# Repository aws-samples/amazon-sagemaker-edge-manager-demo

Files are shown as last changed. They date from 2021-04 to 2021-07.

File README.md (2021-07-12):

# SageMaker Edge Manager demo: Mini wind turbine farm
## A DIY project to explore ML@Edge with SageMaker

 > This repo is part of the blog post [Monitor and Manage Anomaly Detection Models on a fleet of Wind Turbines with Amazon SageMaker Edge Manager](https://aws.amazon.com/blogs/machine-learning/monitor-and-manage-anomaly-detection-models-on-a-fleet-of-wind-turbines-with-amazon-sagemaker-edge-manager/). If you want to implement the full solution, please follow the configuration steps described in the blog post and prepare your AWS account.

**TL:DR**: [Mini 3D printed wind turbines - assembling instructions](ASSEMBLING.md)

> **2021-06-18 NEW**: With the release of SageMaker Edge Manager support in AWS Greengrass v2, we have created a separate branch of this demo. Check it out by doing `git pull & git checkout greengrass`

**DISCLAIMER**: If you don't have a 3D printer or the skills to build your own fleet of wind turbines, don't worry. You can still run the application in demonstration mode. Also, there is a [SageMaker Edge Manager Workshop](https://github.com/aws-samples/amazon-sagemaker-edge-manager-workshop) where you will be able to run a similar experiment but with a Simulator! :)

In this project you'll see how to build a **Mini Wind Turbine Farm**, to experiment with Machine Learning (@ Edge). With a 3D printer and some electronic components you can create a mini Wind Turbine with sensors and a small generator. This project is not intended to be a real-life electricity generator. It's just a device for testing/experimenting real-time and low latency machine learning on edge devices. It was created to demonstrate the capabilities of Amazon SageMaker Edge Manager.

[Amazon SageMaker Edge Manager](https://aws.amazon.com/sagemaker/edge-manager/) allows you to optimize, secure, monitor, and maintain ML models on fleets of smart cameras, robots, personal computers, industrial equipments, mobile devices and more. Using [Amazon SageMaker Edge Manager](https://aws.amazon.com/sagemaker/edge-manager/), you can manage the lifecycle of each ML model on each device in your device fleets for up to thousands or millions of devices. The service provides a software **agent that runs on edge devices** and a management interface in the AWS console. 

Using a Machine Learning model (Autoencoder) you can analyze the turbine sensors data and detect anomalies. This technique is important to improve the maintenance process and reduce the operational cost. Click on the image bellow to see a video of the Wind Turbine Farm running.

<p align="center">
<a href="https://aws-ml-blog.s3.amazonaws.com/artifacts/monitor-manage-anomaly-detection-model-wind-turbine-fleet-sagemaker-neo/wind_farm.mp4">
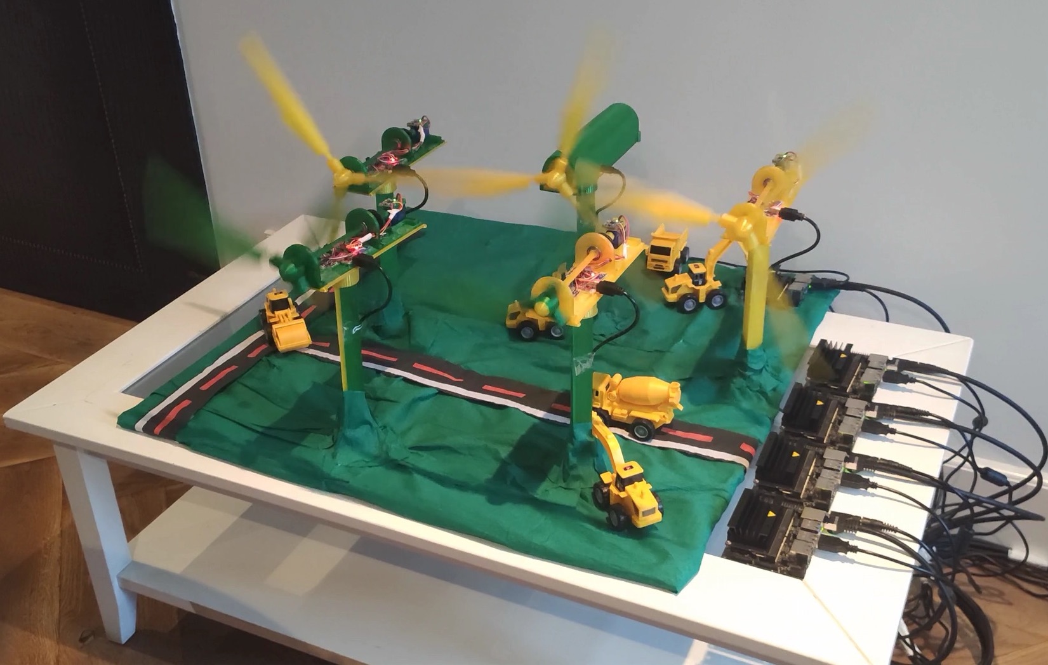
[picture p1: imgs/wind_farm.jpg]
 
</a>
</p>

### Solution architecture
This is the reference architecture of this solution. The idea is to use <a href="https://aws.amazon.com/sagemaker/">Amazon SageMaker</a> to train an [AutoEncoder](https://en.wikipedia.org/wiki/Autoencoder) using the Turbine sensors data. Each edge device (Jetson Nano) has a SageMaker Edge Agent (edge) running on it. The agents are connected to devices registered to a device fleet on SageMaker Edge Manager (cloud). Also, for each edge device there is an IoT Thing. This is required by [the application](/04_EdgeApplication/README.md) that runs on the edge device to send logs to the cloud and for the OTA model update mechanism. By using SageMaker Agent CaptureData, the application collects some metrics from the predictions and sends to an S3 bucket (via agent). Lambda functions process the model metrics from S3 and the app logs from the MQTT Topic and ingests it to Elasticsearch (optional). This data can then be visualized using Kibana.

<p align="center">
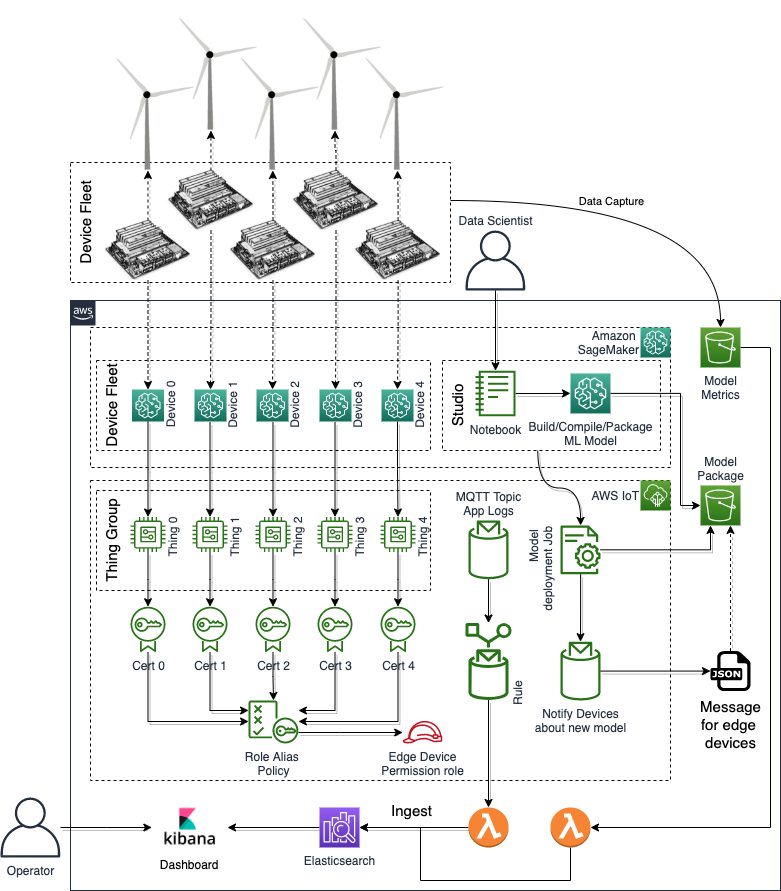
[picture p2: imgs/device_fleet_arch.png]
 
</p>

### Step-by-step
In this repo you'll find instructions of how to build your mini 3D printed Wind Turbines. After that, follow the instructions on the blog post to configure your AWS Account and prepare your mini wind turbine farm. 

In summary, after configuring the your fleet of devices in your AWS Account, these are the steps you need to take to experiment with this solution. 
<p align="center">
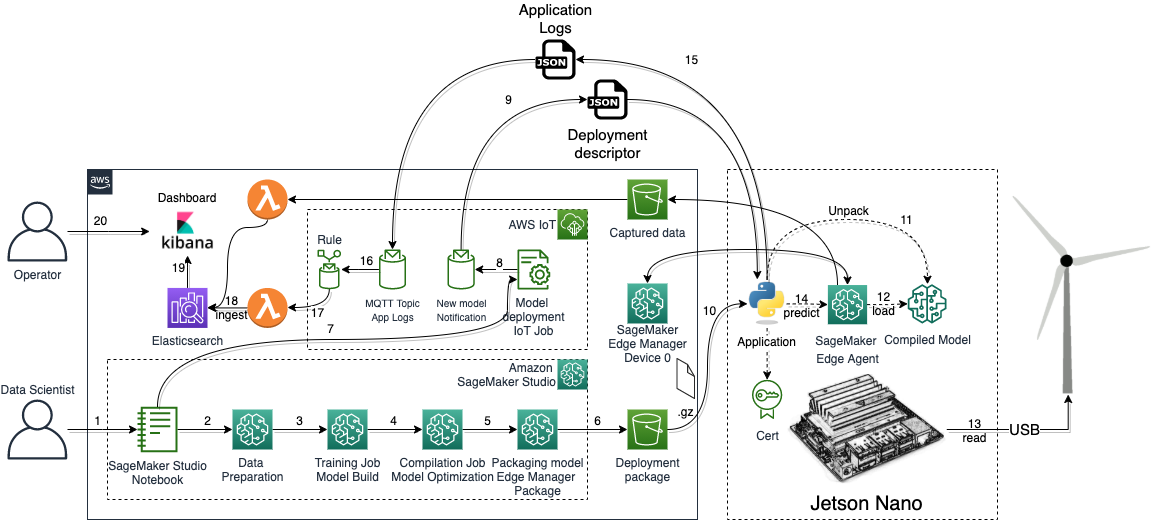
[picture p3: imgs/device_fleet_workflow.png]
 
</p>
  
 1. a data scientist uses SageMaker Studio to prepare a ML model;
 2. the sensors data is prepared: feature selection, cleaning, normalizing, etc.;
 3. using Pytorch, an autoencoder is trained;
 4. using SageMaker Neo, the model is compiled/optimized for Jetson Nano;
 5. using SageMaker Edge Manager, the model is signed and packed with the Jetson Nano runtime;
 6. the packaged is saved to an S3 bucket;
 7. the data scientist creates an IoT Job that sends a notification to the edge application;
 8. using an MQTT topic, which the applications is subscribed to, the message is sent to the edge device;
 9. the application receives a Json document with the model metadata through MQTT;
 10. the application receives the notification and downloads the model package from S3;
 11. the application unpacks the model to a local directory;
 12. the application invokes the agent API LoadModel to load the model (now the model is available to the application);
 13. the application reads some data from the sensors of the Wind Turbine;
 14. the application transform the data and invokes the model using the agent API Predict. Some model metrics are captured by the agent API CaptureData. A Lambda function that listens to that particular bucket, parses the metrics (Json lines) and ingests the data to Elasticsearch;
 15. some application logs are then sent to the cloud trough an MQTT topic;
 16. an IoT Rule reads the application logs;
 17. a lambda function, connected to the IoT Rule, parses the application logs;
 18. the parsed data is then ingested to Elasticsearch;
 19. both model metrics and application logs can be now accessd through Kibana;
 20. using kibana, the operator visualizes anomalies and other information;

### Notebooks
If you didn't configure your SageMaker Studio account yet, [please follow these instructions](https://docs.aws.amazon.com/sagemaker/latest/dg/onboard-quick-start.html) first. Then, clone this repo in Studio. You will run two notebooks there:
  1. [Dataset preparation](03_Notebooks/01%20-%20Data%20Preparation.ipynb): to transform (feature selection, cleaning, denoising, normalizing, etc) the sensors data (raw) into a dataset used to train the model
  2. [Model preparation](03_Notebooks/02%20-%20Training%20with%20Pytorch.ipynb): to train (Pytorch Autoencoder), compile, create a deployment package and notify the edge devices about the new model

### Edge Application
In [this directory](04_EdgeApplication) you'll find the Python application that runs on each Edge Device. Look for the term "the application" in the **Step-by-step** section to understand what it does. This is a custom/standalone application:

[Learn more about the edge application](/04_EdgeApplication)

### Assembling the turbines
Please, [follow the assembling instructions](ASSEMBLING.md).

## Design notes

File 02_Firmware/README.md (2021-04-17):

## Configuring your Arduino IDE to compile a new firmware for your Wind Turbines

If you never used Arduino Before, please visit [this link](https://www.arduino.cc/en/Guide) to download the IDE and learn about how this platform. Inside this directory you will find an Arduino Project. Follow the instructions bellow to configure your environment and then use this project to create a firmware for your Wind Turbines.

### Preparing a package for the Arduino/MPU6050 library
We need to clone and prepare two .zip files with the libraries: MPU6050 and I2CDev. Run the following Bash code to get the library and create the packages.

```bash
# cloning the libaries repo
git clone https://github.com/jrowberg/i2cdevlib

cd i2cdevlib/Arduino/I2Cdev
zip -r ../../../I2Cdev.zip *
cd ../MPU6050
zip -r ../../../MPU6050.zip *

```

### Instaling the required libraries

In your **Arduino IDE**:
  1. Click on **Sketch** --> **Include Library** --> **Manage Libraries...**
  1. Search for **Adafruit BME680**
  1. Select the version **1.1.1** and install
<p align="center">    
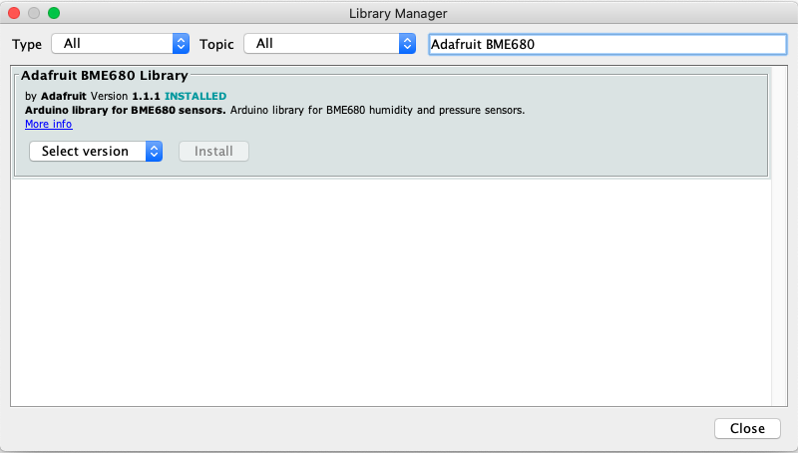
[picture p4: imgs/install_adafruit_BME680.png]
        
</p>

  1. Now, click on **Sketch** --> **Include Library** --> **Add .ZIP Library**
  1. Upload one of the .zip files you created before (I2Cdev.zip or MPU6050.zip)
  1. Repeat this process for the other .zip file

### Modify Adafruit_BME680.cpp
Make sure you installed **Adafruit BME680 version 1.1.1** before executing this step.  
Open the local directory where Aduino installs libraries. If you're using a MacOS/Linux machine, this is the dir:  
**~/Documents/Arduino/libraries/**  

Edit the following file and comment line 129: **Adafruit_BME680_Library/Adafruit_BME680.cpp**  
 
**From**:  
 ```c++
 _wire->begin();
 ```

**To**:
```c++
//_wire->begin();
```

### Select the correct board
In your **Arduino IDE**:
  1. Click on **Tools** --> **Board** --> **Arduino AVR Boards** --> **Arduino Pro or Pro Mini**
  1. Then click on **Tools** --> **Processor** --> **ATmega382P (3.3, 8MHz)**
  2. Connect your board to the computer using an FTDI module;
  3. Then select the correct port by clicking on: **Tools** --> **Port** --> **<<port_used_by_arduino>>**

<p align="center">    
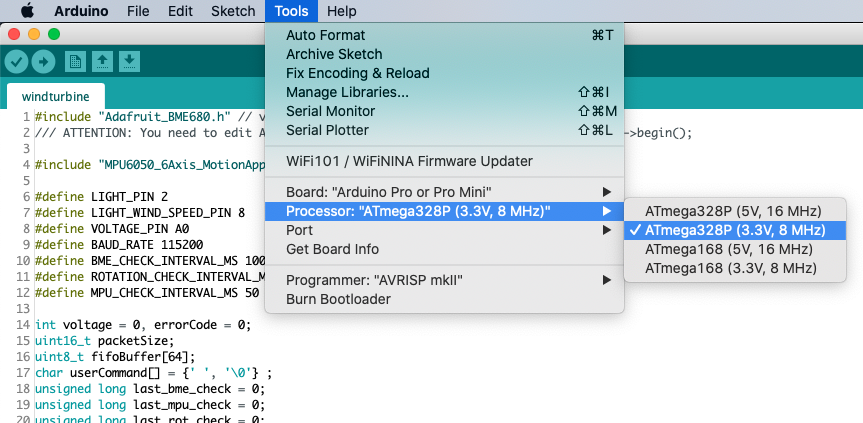
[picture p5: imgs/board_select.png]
        
</p>

Now your environment is ready to compile the firmware. Load the arduino project from this folder, compile it and upload it to your arduino.

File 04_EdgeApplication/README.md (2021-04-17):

## Edge application

This is a Python application that runs on the Edge device. It connects all the components together and is reponsible for the loop that reads the sensors data, prepare the data, invoke the ML model and report back to the cloud metrics and logs.

This is the reference architecture of this application:
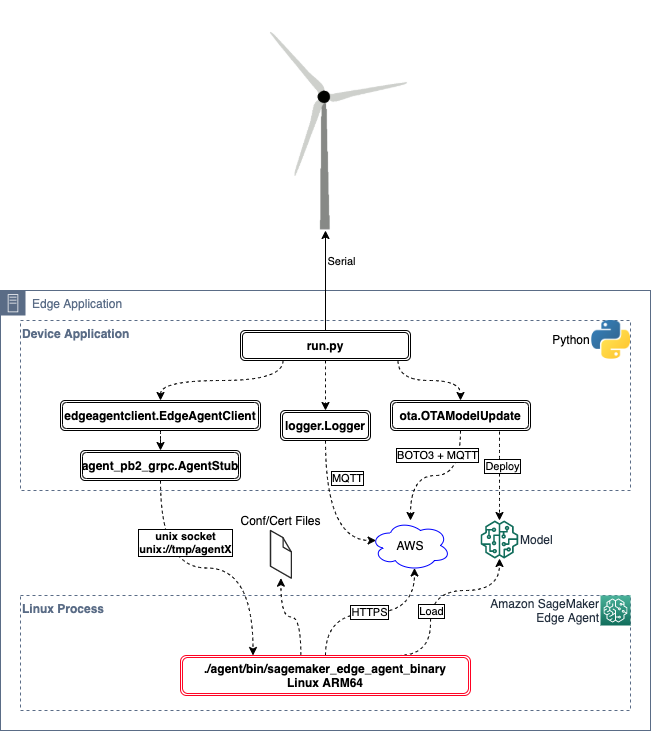
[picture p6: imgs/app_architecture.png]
Application Architecture


As you can see, the application has some Python modules responsible for:
 - **run.py**: main application that launches all the other components
 - **EdgeAgentClient**: client that communicates with SageMaker Edge Agent, using protobuf/grpc
 - **AgentStubs**: Python stubs generated by the protobuf compiler
 - **Logger**: module responsible for buffering application logs and then sending this data to the cloud via MQTT
 - **OTAModelUpdate**: module that subscribes to special MQTT topics, gets notifications of new models and deploys the models to the edge device

### Running the application
You can run this application manually or using the bash scripts that start/stop the agent and the application.

**Manual execution**

```bash
$ ./run.py -h
usage: run.py [-h] [--test-mode] [--inject-noise] [--debug]
              [--agent-socket AGENT_SOCKET] [--model-path MODEL_PATH]
              [--serial-port SERIAL_PORT] [--serial-baud SERIAL_BAUD]
              [--sagemaker-edge-configfile-path SAGEMAKER_EDGE_CONFIGFILE_PATH]

optional arguments:
  -h, --help            show this help message and exit
  --test-mode           Use a dummy file as sensors readings
  --inject-noise        Add random noise to the raw data
  --debug               Enable debugging messages
  --agent-socket AGENT_SOCKET
                        The unix socket path created by the agent
  --model-path MODEL_PATH
                        Absolute path to the model dir
  --serial-port SERIAL_PORT
                        Path to the USB port used by the wind turbine
  --serial-baud SERIAL_BAUD
                        Serial comm. speed in bits per second
  --sagemaker-edge-configfile-path SAGEMAKER_EDGE_CONFIGFILE_PATH
                        Path to the agent config file
```

All the parameters are optional. By default, it will use an env var **SM_EDGE_AGENT_HOME** that points to the dir where you installed SageMaker Edge Agent.

Test mode: if you pass **--test-mode** the application will download a dummy file and use it as the sensors readings. You don't need the real wind turbines connected to the edge device in this mode.

**Bash scripts**

 - [app_start.sh](/04_EdgeApplication/scripts/app_start.sh): initialize two background processes; one for the agent and another for the application. You can also invoke this script to make sure your application is still running. It checks a **PID** file to see if the processes are running;
 - [app_stop.sh](/04_EdgeApplication/scripts/app_stop.sh): kills both processes; the agent and the app.

## Reports/dashboards

[Find here](/04_EdgeApplication/report) instructions to plug your wind turbine farm application to a report tool. You'll see how to use Elastisearch/Kibana or AWS CloudWatch to visualize anomalies and other info related to your turbines.

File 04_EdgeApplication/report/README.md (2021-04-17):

# AWS Lambda functions for ingesting data into your report tool

If you want to visualize the anomalies and the logs, you can use one these lambda functions to ingest data into Elasticsearch or CloudWatch Logs.

The lambdas need to be 'configured' to capture 'Put' events in the S3 bucket, used by SageMaker Edge Agent to store data (CaptureData). For each Json lines file stored in this bucket the Lambda function will parse it and send the data to the chosen report tool. Also, for the application logs, sent by the application to an MQTT topic, you need to configure an IoT Rule that will capture the data (with the following query) and invoke the same Lamda function:
```sql
SELECT 'logs' as msg_type, topic(3) as device_name, * FROM 'wind-turbine/logs/#' 
```

## Elastisearch + Kibana
You need to create two indices in your Elasticsearch first. In the Kibana console, go to 'Dev Tools', copy and paste the following content and run:
```html
PUT wind_turbine_logs
{
  "mappings": {
    "data": {
      "properties": {
        "eventTime": {
          "type": "date",
          "format": "strict_date_time"
        },
        "deviceId": {
           "type": "keyword"
        }
      }
    }
  }
}

PUT wind_turbine_preds
{
 "mappings": {
    "data": {
      "properties": {
        "eventTime": {
          "type": "date",
          "format": "strict_date_time"
        },
        "deviceId": {
           "type": "keyword"
        }
      }
    }
  }
}
```
This [Lambda](/04_EdgeApplication/setup/lambda_ingest_logs_elasticsearch.py) requires an environment variable, that needs to be defined in the AWS Lambda console, while you're creating this function:
```bash
ELASTIC_SEARCH_URL = https://<<YOUR_ELASTICSEARCH_DOMAIN_PREFIX_HERE>>.<<REGION>>.es.amazonaws.com
```

<table>
  <tr>
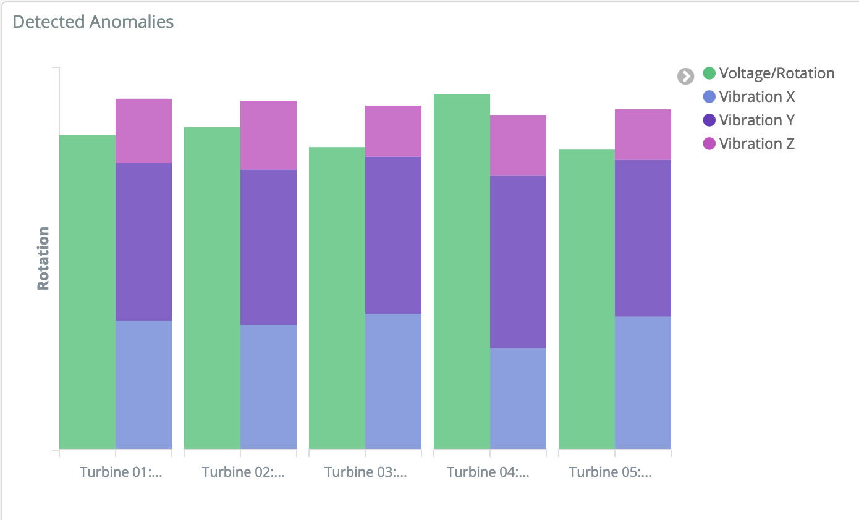
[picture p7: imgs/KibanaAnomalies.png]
    <td></td>
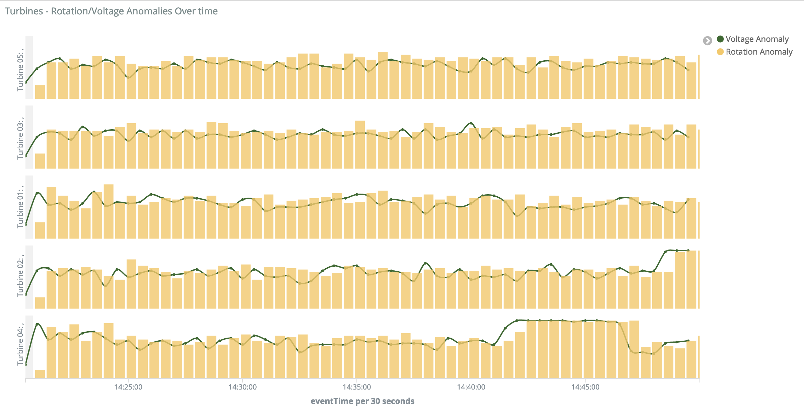
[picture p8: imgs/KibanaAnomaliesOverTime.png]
    <td></td>
  </tr>
</table>

## CloudWatch
This [Lambda](/04_EdgeApplication/setup/lambda_ingest_logs_cloudwatch.py) requires that you first create, in your AWS CloudWatch Logs console, a log group named **/wind-turbine-farm**. Then, inside this log group, create two **log streams**: preds and sensors.

Now, after start ingesting data to these log streams, you can create queries and dashboards. Some examples of queries:

### Rotation Avg
```sql
parse '* * * * * * * * * * * * * * * * * * * * * *' as
  ts, device_name, arduino_timestamp, arduino_freemem, rps, wind_speed_rps,
    voltage, qw, qx, qy, qz, gx, gy, gz, aax,aay,aaz, gearbox_temp, ambient_temp,
    air_humidity, air_pressure, air_quality
    | filter @logStream like /sensors/
    | sort @timestamp desc
    | limit 20
    | stats avg(rps) as rps_avg,
            avg(wind_speed_rps) as wind_speed_rps_avg
            by bin(1m)
```
### Voltage Avg
```sql
parse '* * * * * * * * * * * * * * * * * * * * * *' as
  ts, device_name, arduino_timestamp, arduino_freemem, rps, wind_speed_rps,
    voltage, qw, qx, qy, qz, gx, gy, gz, aax,aay,aaz, gearbox_temp, ambient_temp,
    air_humidity, air_pressure, air_quality
    | filter @logStream like /sensors/
    | sort @timestamp desc
    | limit 20
    | stats avg(voltage) as voltage_avg
            by bin(1m)
```
### Vibration Avg
```sql
parse '* * * * * * * * * * * * * * * * * * * * * *' as
  ts, device_name, arduino_timestamp, arduino_freemem, rps, wind_speed_rps,
    voltage, qw, qx, qy, qz, gx, gy, gz, aax,aay,aaz, gearbox_temp, ambient_temp,
    air_humidity, air_pressure, air_quality
    | filter @logStream like /sensors/
    | sort @timestamp desc
    | limit 20
    | stats avg(qw) as qw_avg,
            sum(qx) as qx_avg,
            avg(qy) as qy_avg,
            avg(qz) as qz_avg
            by bin(1m)
```
### Anomalies Count
```sql
parse '* * * * * * * * * * * *' as 
  roll_mae, pitch_mae, yaw_mae, wind_mae, rps_mae, voltage_mae, 
  roll_anom, pitch_anom, yaw_anom, wind_anom, rps_anom, voltage_anom
| filter @logStream like /preds/
| sort @timestamp desc
| limit 20
| stats sum(roll_anom) as roll_anomalies, 
        sum(pitch_anom) as pitch_anomalies,
        sum(yaw_anom) as yaw_anomalies,
        sum(wind_anom) as wind_anomalies,
        sum(rps_anom) as rps_anomalies,
        sum(voltage_anom) as voltage_anomalies
        by bin(1m)
| sort maxBytes desc
```

<table>
  <tr>
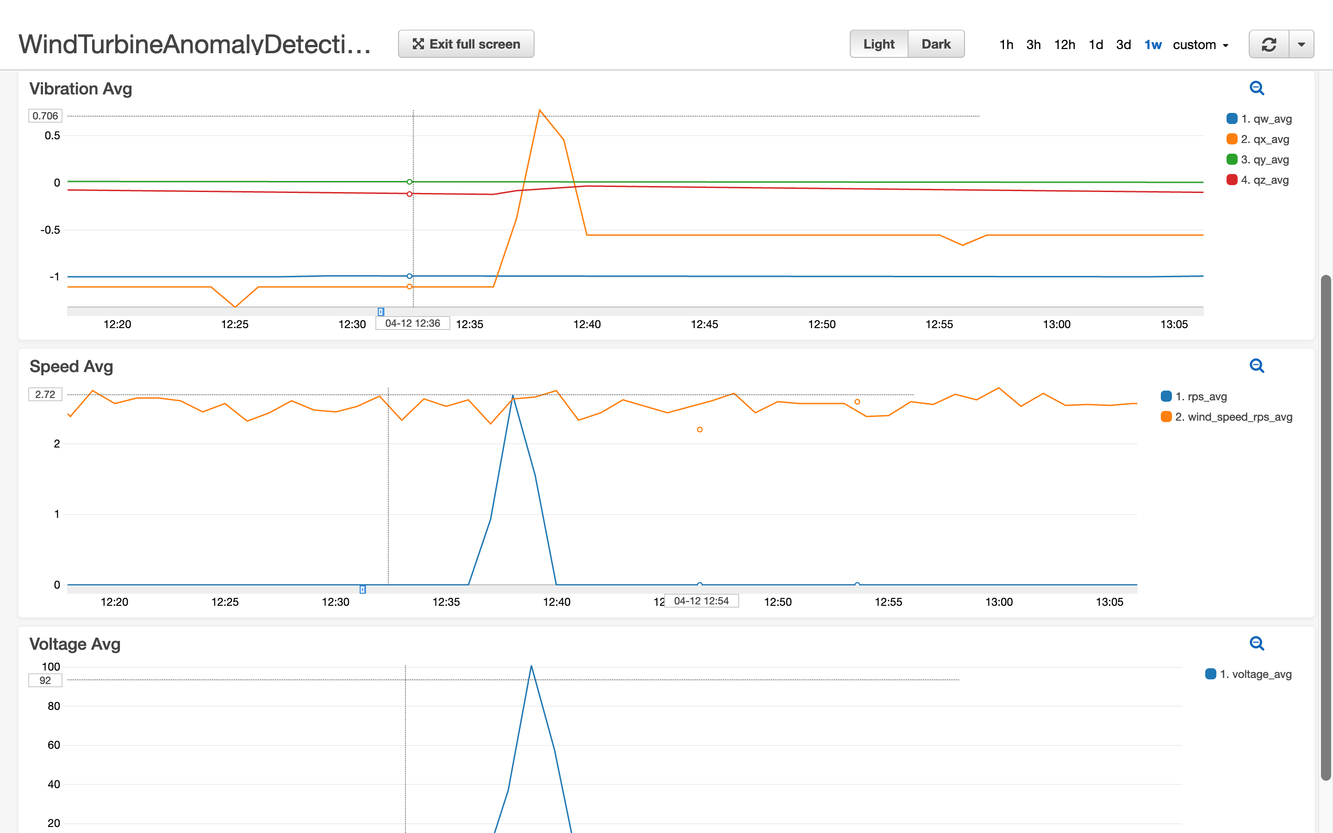
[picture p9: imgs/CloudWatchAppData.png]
    <td></td>
  </tr>
</table>

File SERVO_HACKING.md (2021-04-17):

## Hacking a mini servo 9G to transform it into a small voltage generator

This a Servo normal servo 9G, composed by: a DC motor, a gearbox and a motor driver board. In order to use this device in the WindTurbine we need to hack it.
By hacking I mean to convert the servo into a simple Generator. 
<p align="center">
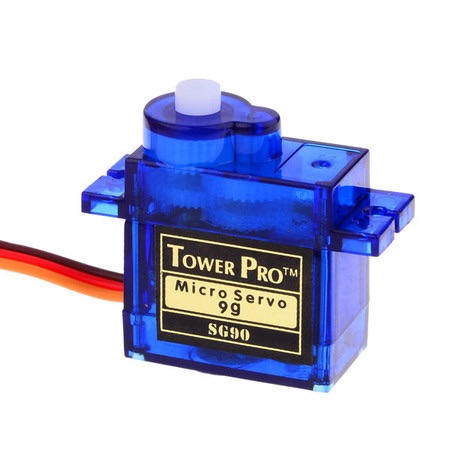
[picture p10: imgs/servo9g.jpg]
      
</p>

The hack is basically the following steps:
 - 3D print the [Servo Shaft](01_3DModels/stl/big_shaft.stl) and the [Small Generator Connector](01_3DModels/stl/small_generator_connector.stl)
 - disassemble the servo
 - remove the shaft/gear and the second gear (#1 and #2 in the image bellow). Keep only the two gears close to the motor.
 - remove the driver board
 - solder back to the DC motor only positive and negative
 - remove the potentiometer upper part (you need to break it)
 - glue the Servo Shaft (with super glue) to gear #3 (image bellow)
 - put everything back to the case and close it
 - plug the **Small Generator Connector** to the **Servo Shaft**

<p align="center">
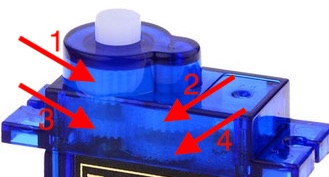
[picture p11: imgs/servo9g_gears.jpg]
 
</p>

You can see the steps in the pictures bellow:
<table border="0" align="center">
    <tr>
      <td>
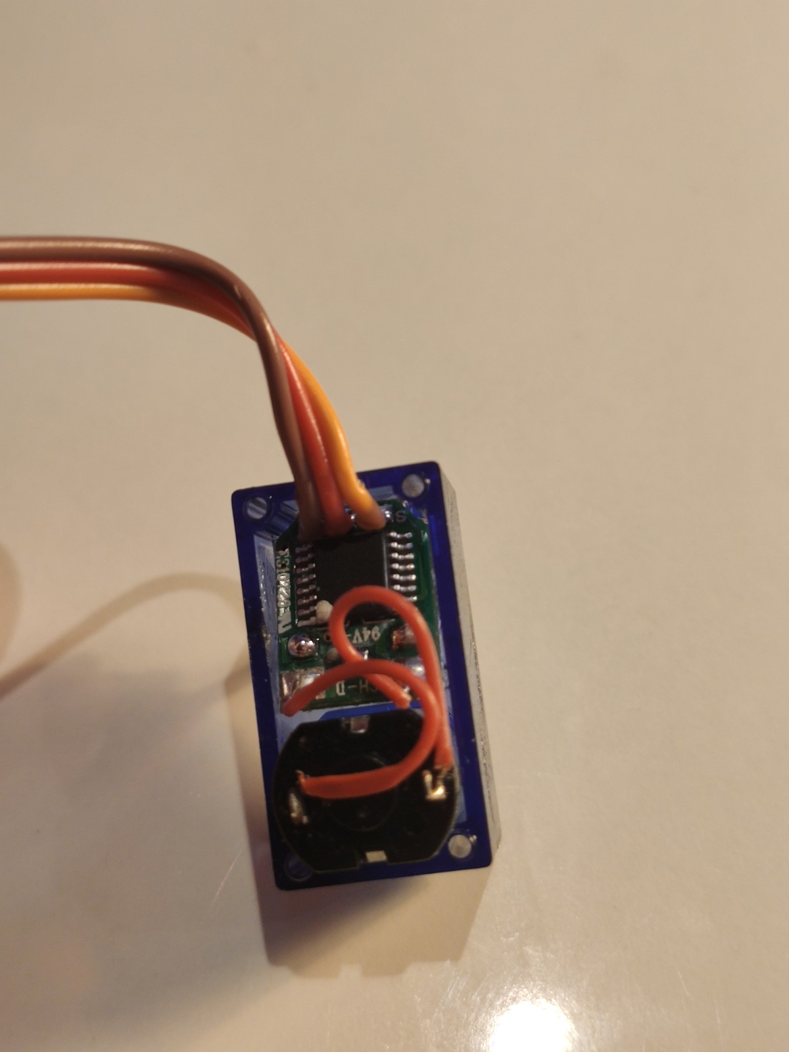
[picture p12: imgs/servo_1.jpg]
        
      </td>
      <td>
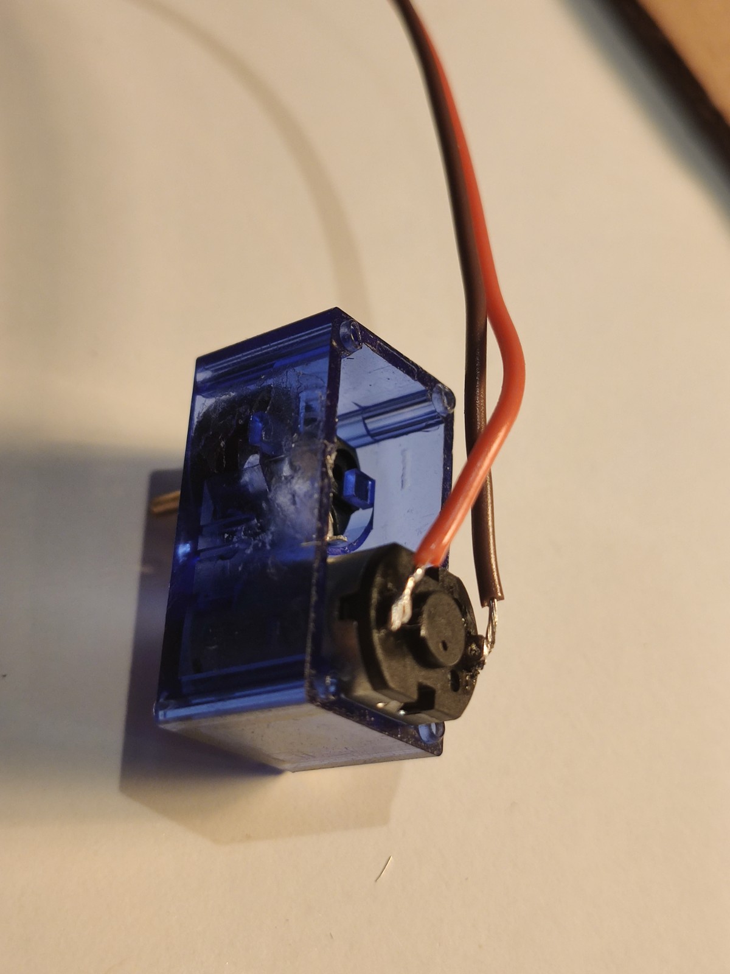
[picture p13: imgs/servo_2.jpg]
        
      </td>
      <td>
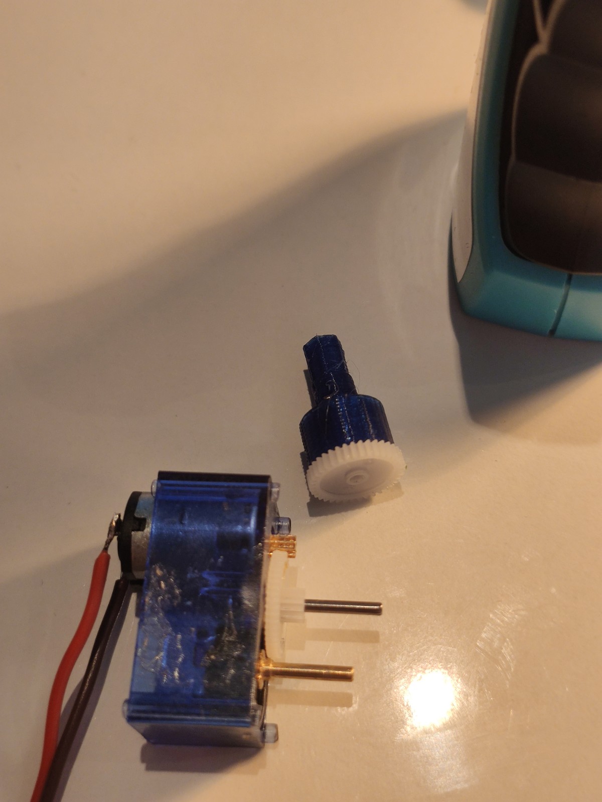
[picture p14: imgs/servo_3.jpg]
        
      </td>
    </tr>
    <tr>
      <td>
        Open the servo and remove the driver board. Keep the cable.
      </td>
      <td>
        Solder the cable directly to the motor. Pay attention to the polarity.
      </td>
      <td>
        Keep gears 3 and 4 (check the image above) and glue gear 3 to the Servo shaft.
      </td>
    </tr>
    <tr>
      <td>
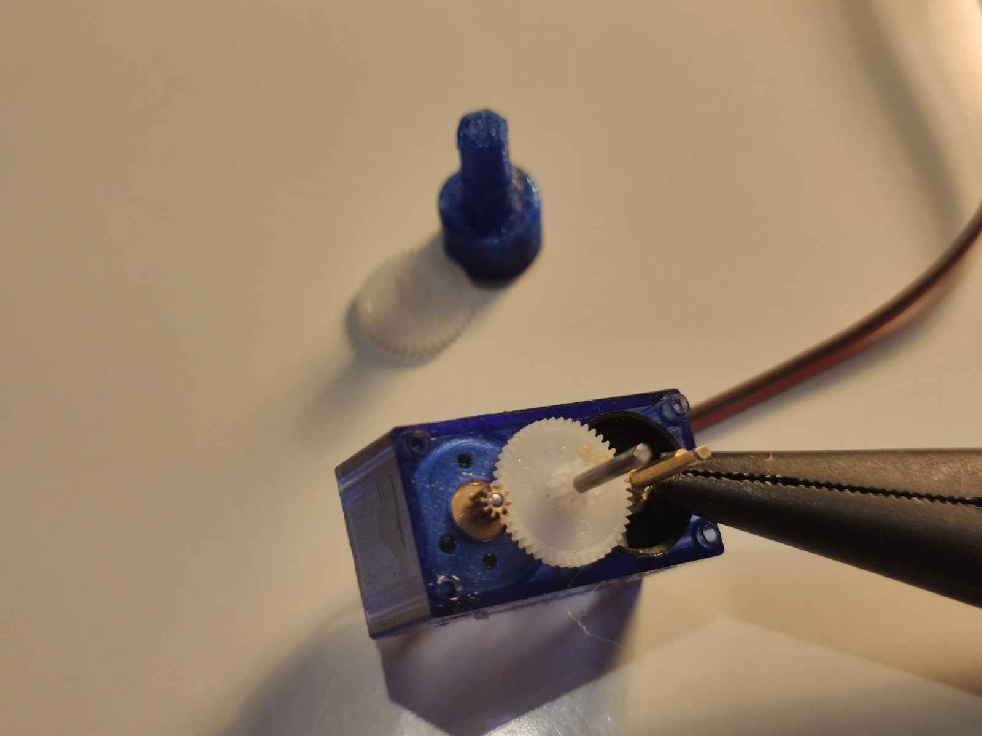
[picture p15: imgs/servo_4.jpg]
        
      </td>
      <td>
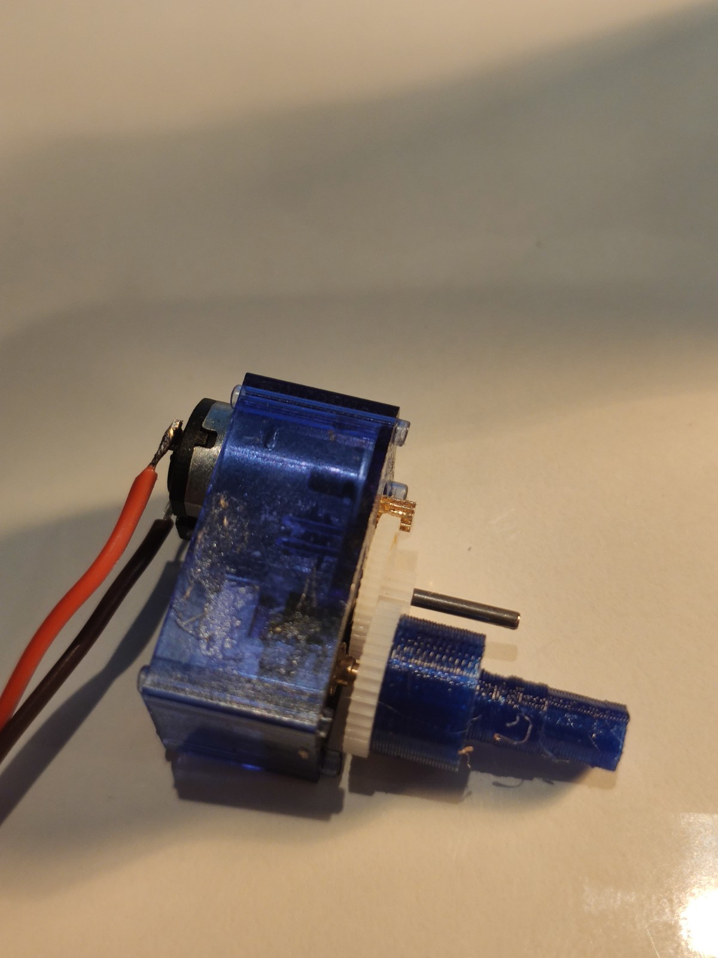
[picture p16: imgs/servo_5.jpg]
        
      </td>
      <td>
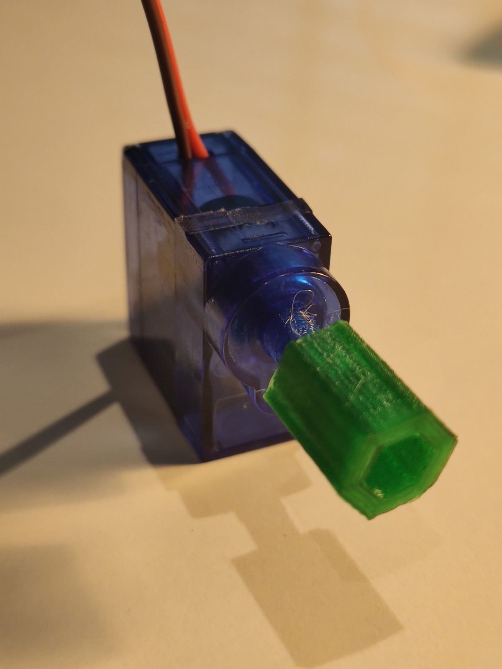
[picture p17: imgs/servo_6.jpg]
        
      </td>
    </tr>
    <tr>
      <td>
        Remove (break & pull) the potentiometer to reduce the friction.
      </td>
      <td>
        Put the glued gear 3 back.
      </td>
      <td>
        Put the servo case back and attach the **Small Generator Connector** to the new Servo Shaft.
      </td>
    </tr>
</table>

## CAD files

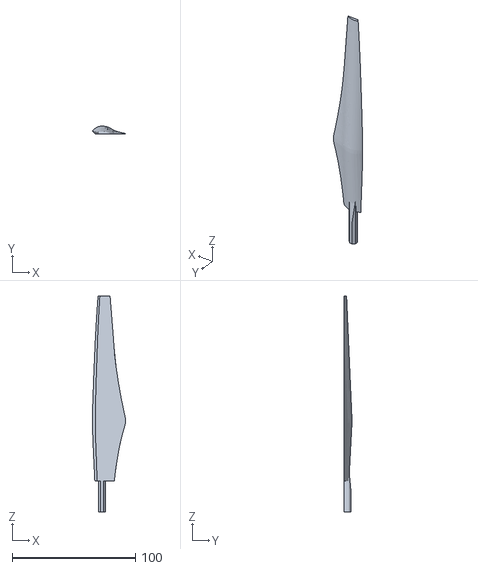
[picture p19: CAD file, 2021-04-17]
01_3DModels/stl/full_blade.stl
27.0 x 6.44 x 175.0

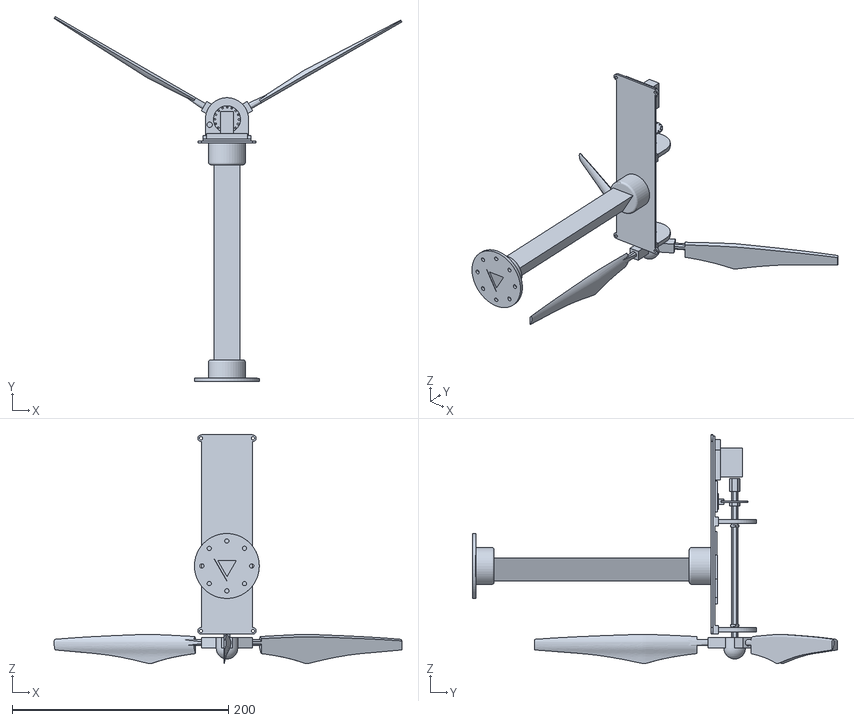
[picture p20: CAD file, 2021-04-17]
01_3DModels/stl/full_turbine.stl
321.5 x 337.3 x 211.7

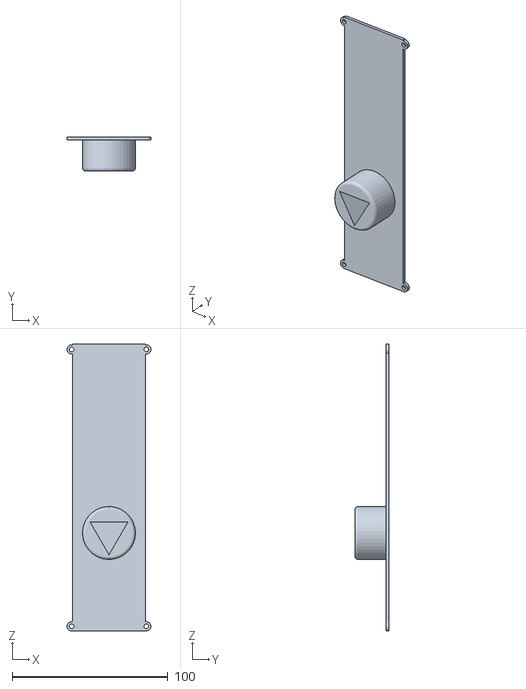
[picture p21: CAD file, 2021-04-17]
01_3DModels/stl/body_support_static.stl
54.0 x 22.0 x 184.5

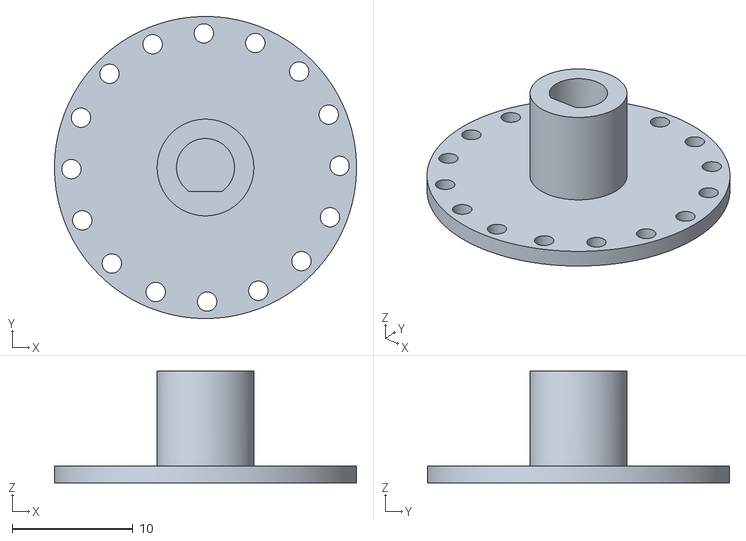
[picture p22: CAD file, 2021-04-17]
01_3DModels/wind_speed_stl/light_disc.stl
25.0 x 25.0 x 9.25

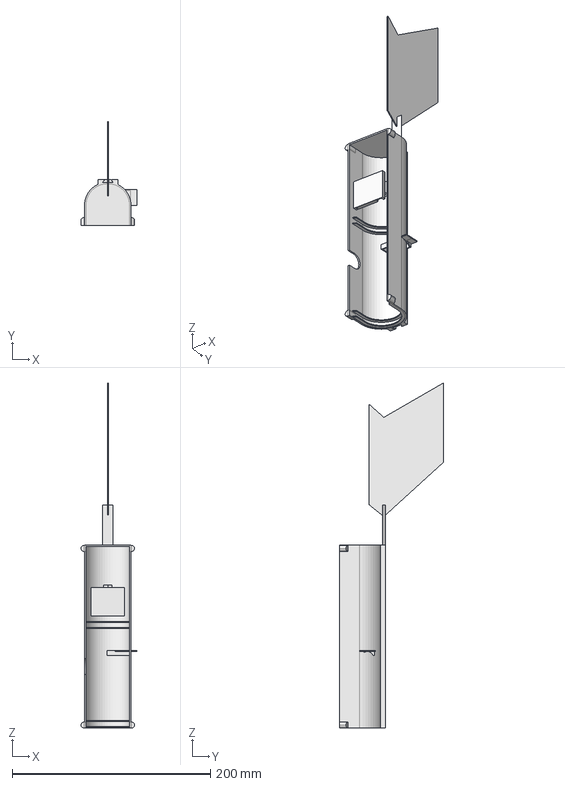
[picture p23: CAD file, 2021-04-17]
01_3DModels/WindTurbine.FCStd
56.5 x 104.5 x 347.6 mm
03_SmallGeneratorConnector
08_LightSensorSupport
10_MPU6050Support
16_BodyCover
17_WindStabilizerConnector
18_WindStabilizer

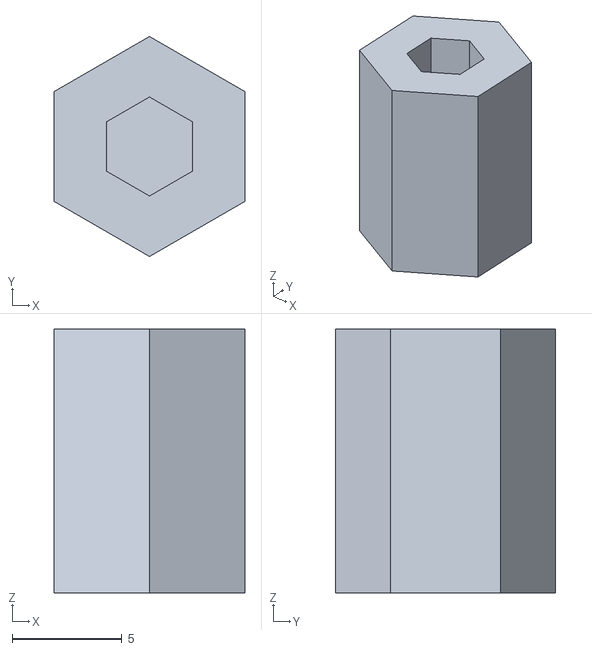
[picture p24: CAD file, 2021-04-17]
01_3DModels/stl/small_generator_connector.stl
8.66 x 10.0 x 12.0

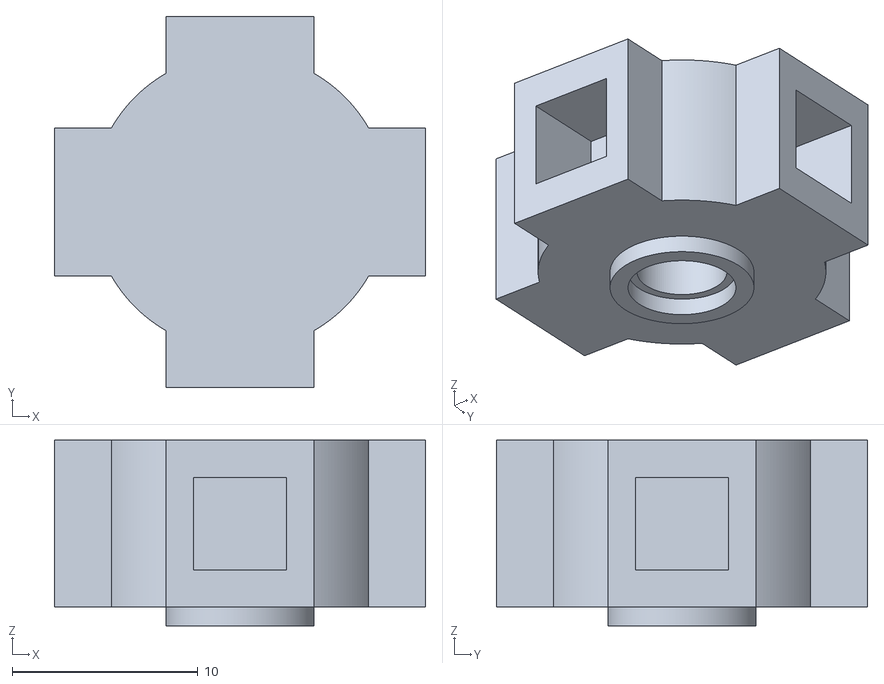
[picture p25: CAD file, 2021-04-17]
01_3DModels/wind_speed_stl/rotor.stl
20.0 x 20.0 x 10.0

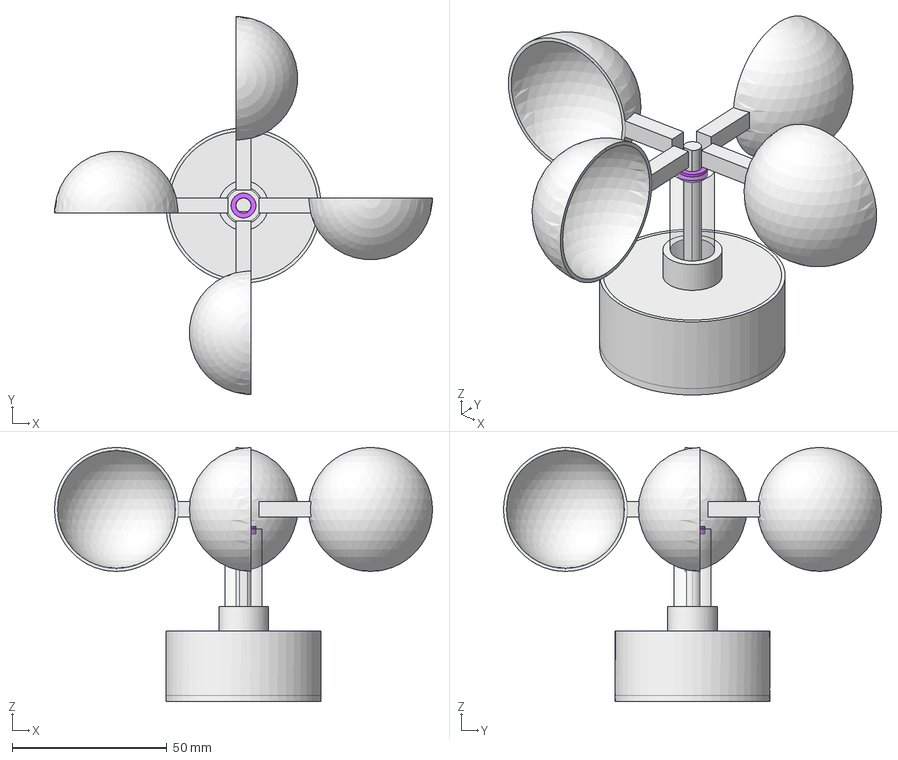
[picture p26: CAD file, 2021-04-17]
01_3DModels/WindSpeed.FCStd
122.0 x 122.0 x 82.0 mm
BladeA
BladeB
BladeC
BladeD
ShaftCover
Shaft
BearingA
BearingB
LightSensor
LightDisc
BoxCover
LightSensorSupport

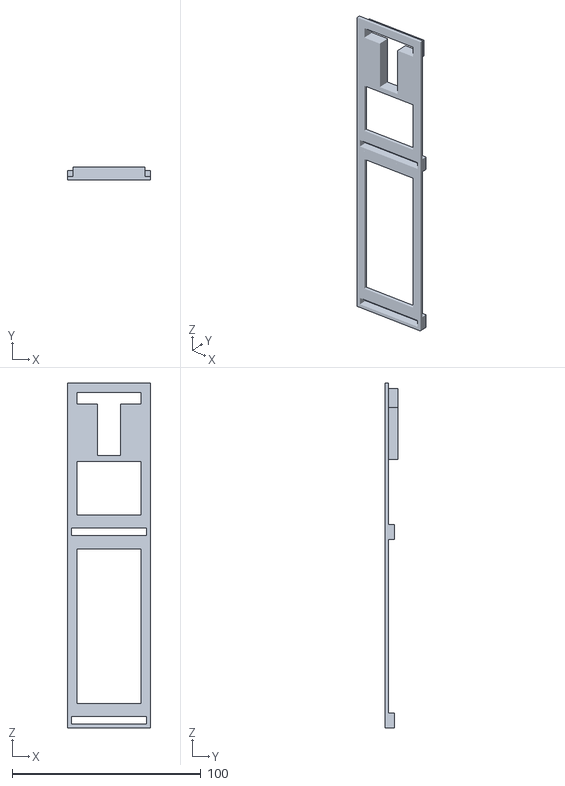
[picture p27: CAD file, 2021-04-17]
01_3DModels/stl/box_base.stl
44.0 x 7.00 x 183.0

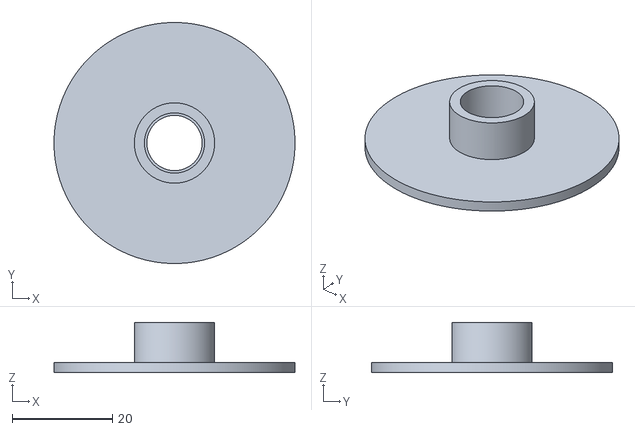
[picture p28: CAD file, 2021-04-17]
01_3DModels/wind_speed_stl/box_cover.stl
48.0 x 48.0 x 10.0

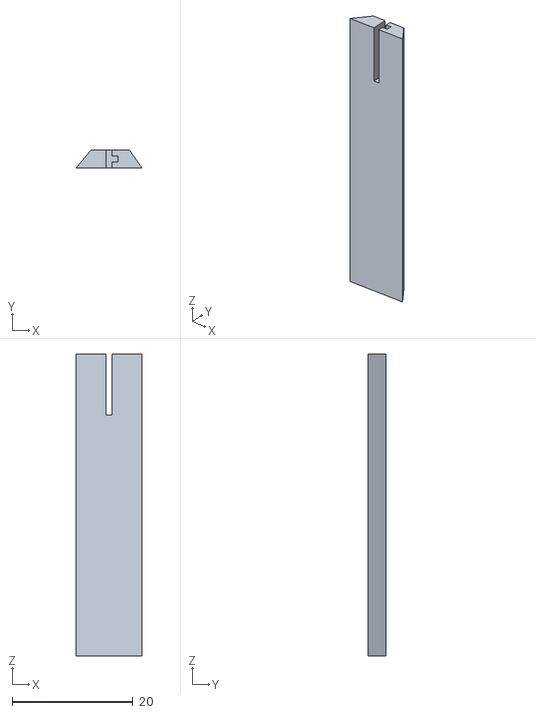
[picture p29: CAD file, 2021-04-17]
01_3DModels/stl/wind_stabilizer_connector.stl
10.9 x 3.00 x 50.0

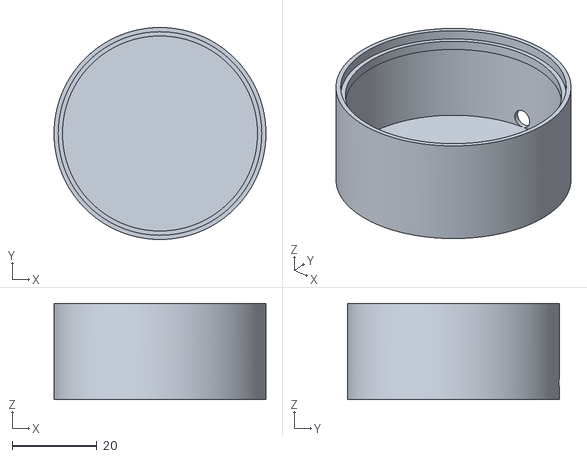
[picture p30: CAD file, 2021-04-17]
01_3DModels/wind_speed_stl/box.stl
50.0 x 50.0 x 22.8

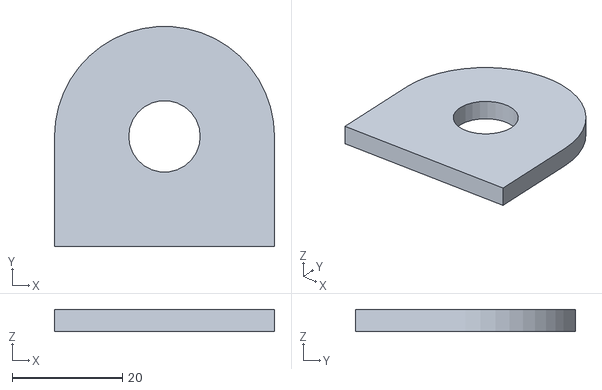
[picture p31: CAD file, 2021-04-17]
01_3DModels/stl/pillar_b.stl
40.0 x 40.0 x 4.00

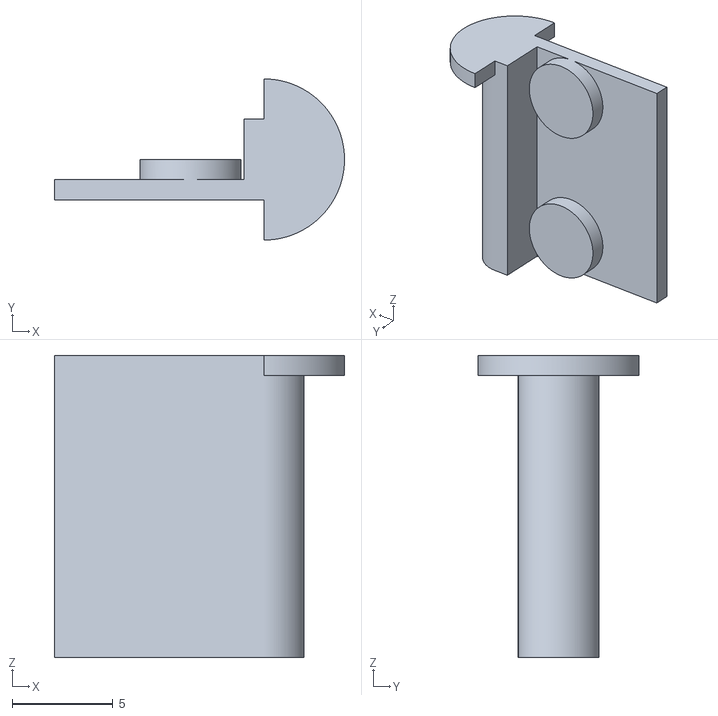
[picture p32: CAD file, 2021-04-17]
01_3DModels/wind_speed_stl/light_sensor_support.stl
14.4 x 8.00 x 15.0

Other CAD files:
01_3DModels/stl/pole_triangle.stl
01_3DModels/wind_speed_stl/shaft.stl
01_3DModels/stl/servo_shaft.stl
01_3DModels/wind_speed_stl/blade.stl
01_3DModels/stl/bearing_plug.stl
01_3DModels/stl/big_shaft.stl
01_3DModels/stl/body_cover.stl
01_3DModels/stl/body_support_dynamic.stl
01_3DModels/stl/light_disc.stl
01_3DModels/stl/light_sensor_support.stl
01_3DModels/stl/mpu_support.stl
01_3DModels/stl/pillar_a.stl
01_3DModels/stl/pole_base.stl
01_3DModels/stl/rotor_base.stl
01_3DModels/stl/sensors_bed.stl
01_3DModels/stl/wind_stabilizer.stl
01_3DModels/wind_speed_stl/shaft_cover.stl

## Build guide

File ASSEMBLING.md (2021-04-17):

## Building your own mini wind turbine

A Mini Wind Turbine is composed by 3D printed parts and some electronic components. It is static, which means that it doesn't align itself with the wind direction.
Also, it requires an USB cable for energy and data transfer.
<p align="center">
  <table border="0" align="center">
    <tr>
      <td>
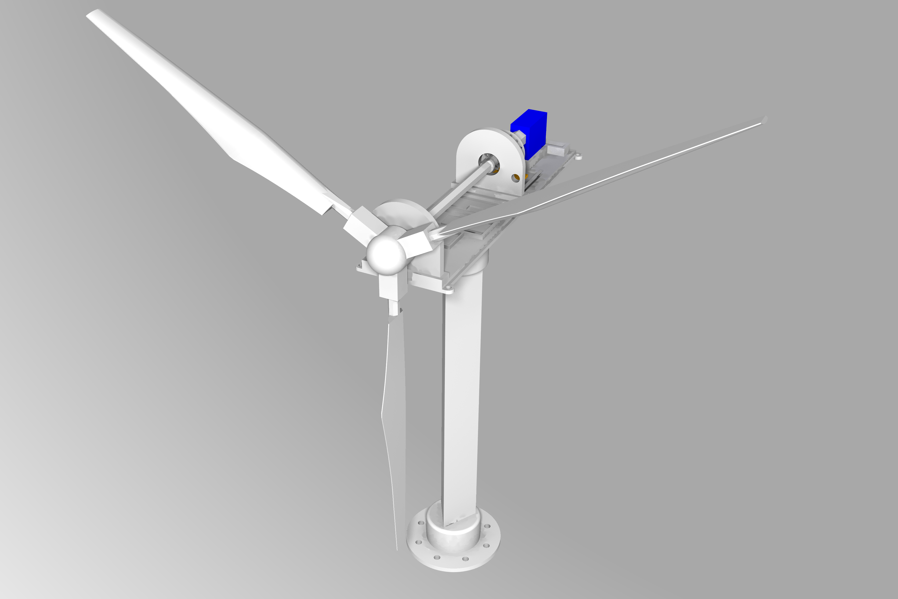
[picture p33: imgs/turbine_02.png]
        
      </td>
      <td>
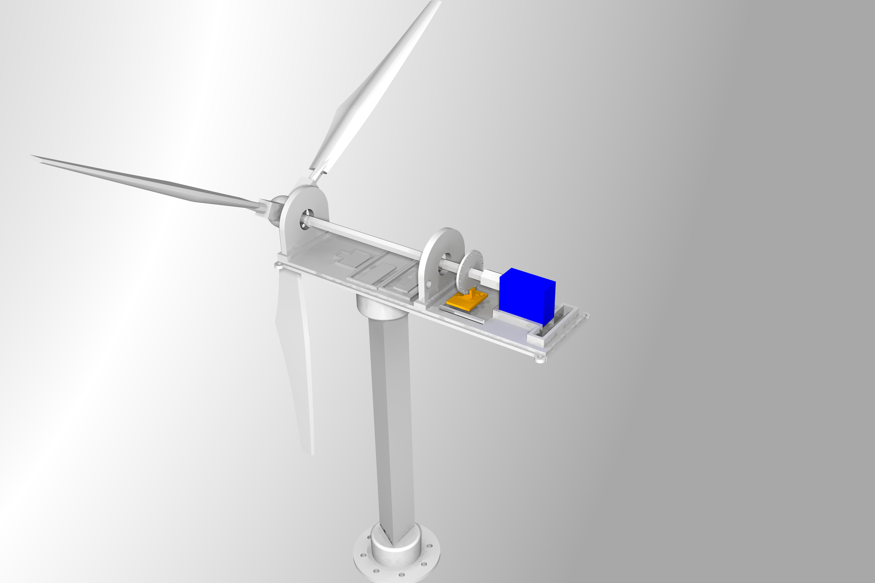
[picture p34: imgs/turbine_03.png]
        
      </td>
    </tr>
  </table>  
</p>

Get and 3D print the following parts:
  - [Shaft](01_3DModels/stl/big_shaft.stl)
  - [Servo/Generator Shaft](01_3DModels/stl/servo_shaft.stl)
  - [Body Cover](01_3DModels/stl/body_cover.stl)
  - [Body Support](01_3DModels/stl/body_support_static.stl)
  - [Box Base](01_3DModels/stl/box_base.stl)
  - [Blade x3](01_3DModels/stl/full_blade.stl)  
  - [Light Disc](01_3DModels/stl/light_disc.stl)
  - [Light Sensor Support](01_3DModels/stl/light_sensor_support.stl)
  - [MPU Support](01_3DModels/stl/mpu_support.stl)
  - [Pillar A](01_3DModels/stl/pillar_a.stl)
  - [Pillar B](01_3DModels/stl/pillar_b.stl)
  - [Pole Base](01_3DModels/stl/pole_base.stl)
  - [Pole](01_3DModels/stl/pole_triangle.stl)
  - [Rotor Base](01_3DModels/stl/rotor_base.stl)
  - [Sensors Bed](01_3DModels/stl/sensors_bed.stl)
  - [Small Generator Connector](01_3DModels/stl/small_generator_connector.stl)

There is no PCB for this project. All the components are soldered with wires and glued (hot glue) to the turbine. Take a look on the following schematics:
<p align="center">
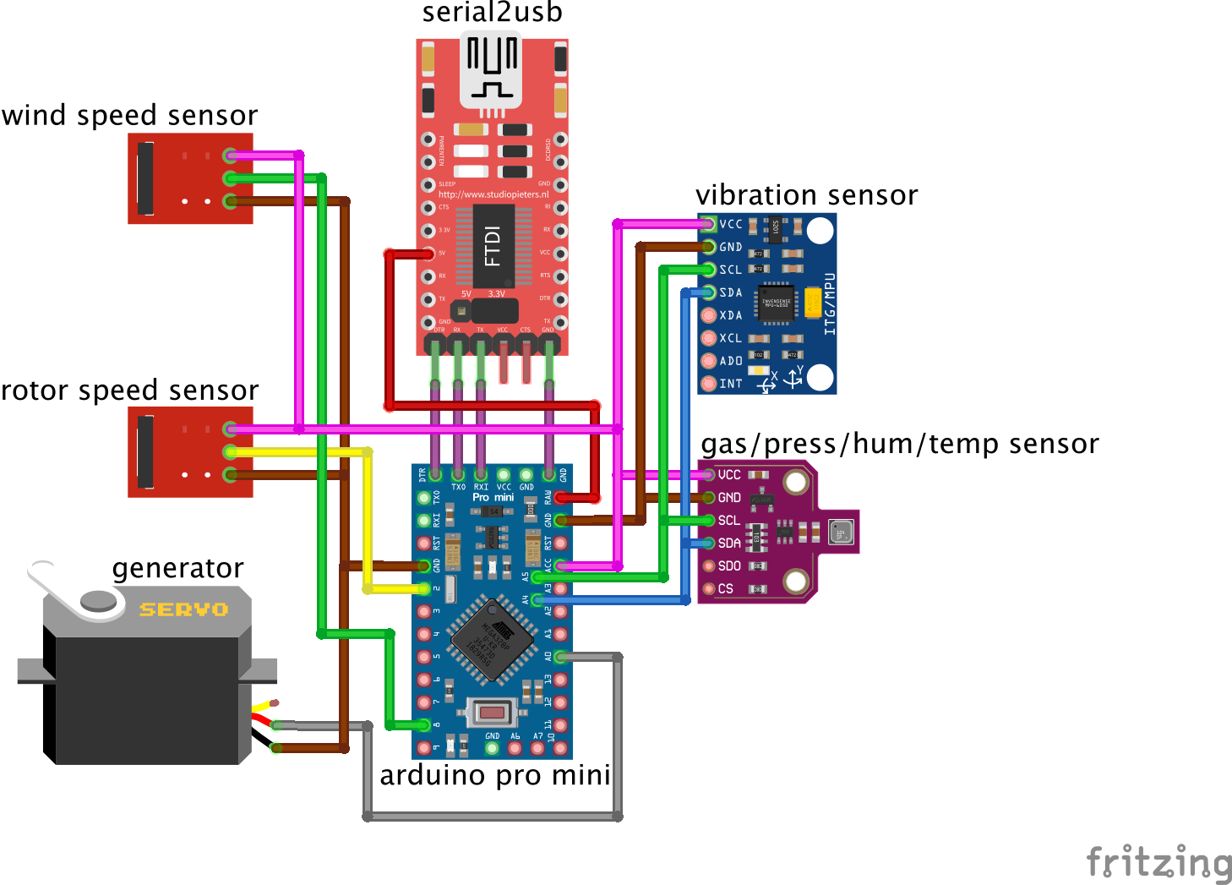
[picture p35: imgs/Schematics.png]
  
</p>

As you can see, the turbine is based on **Arduini Mini Pro 3v3**. The other components are:
  - **BME680**: a sensor for temperature, air pressure, air quality and humidity
  - **MPU6050**: an (6axis) accelerometer + gyroscope used for vibration analisys
  - **FTDI generic USB to serial converter**: configured with 3v3v, but 5V is applied to the **RAW** (regulated) terminal of the Arduino
  - **Generator - Hacked servo 9G**: this is a common servo 9g without the driver board and with modified gears. **[Click here](SERVO_HACKING.md)** to see how to hack your servo.
  - **Speed Encoder - Photo interrupter [Keyes K-010](https://www.amazon.de/-/en/AZDelivery-Sensor-Parent-KY-Kit/dp/B07DQLPZYF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)**: To count how many rotations per second 
  - **F686ZZ Flanges Radial KUGELL Bearings/ [Shielded Flange Ball Bearing 6 x 13 x 5 mm](https://www.amazon.de/gp/product/B078R9JJDY/ref=ppx_yo_dt_b_asin_title_o04_s00?ie=UTF8&psc=1) x2**: two ball bearings to connect the shaft to the pillars.

<p align="center">
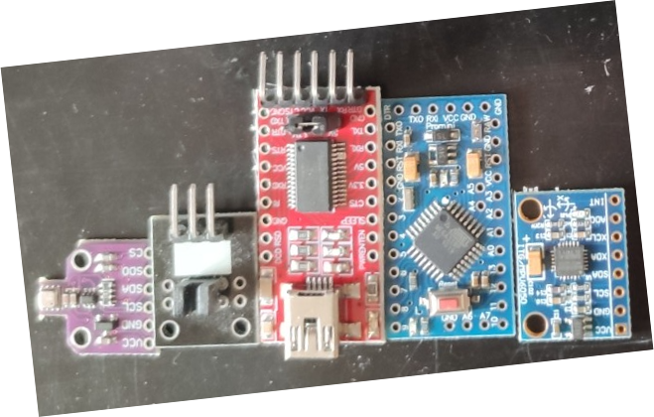
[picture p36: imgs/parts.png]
  
</p>

Take a look on the pictures bellow to see how to put everything together. Use the schematics above to solder all the components. Just put pressure on some parts to attach them on each other. Use **hot glue** to fix the moving parts as shown in the pictures.
 
   <table border="0" align="center">
    <tr>
      <td>
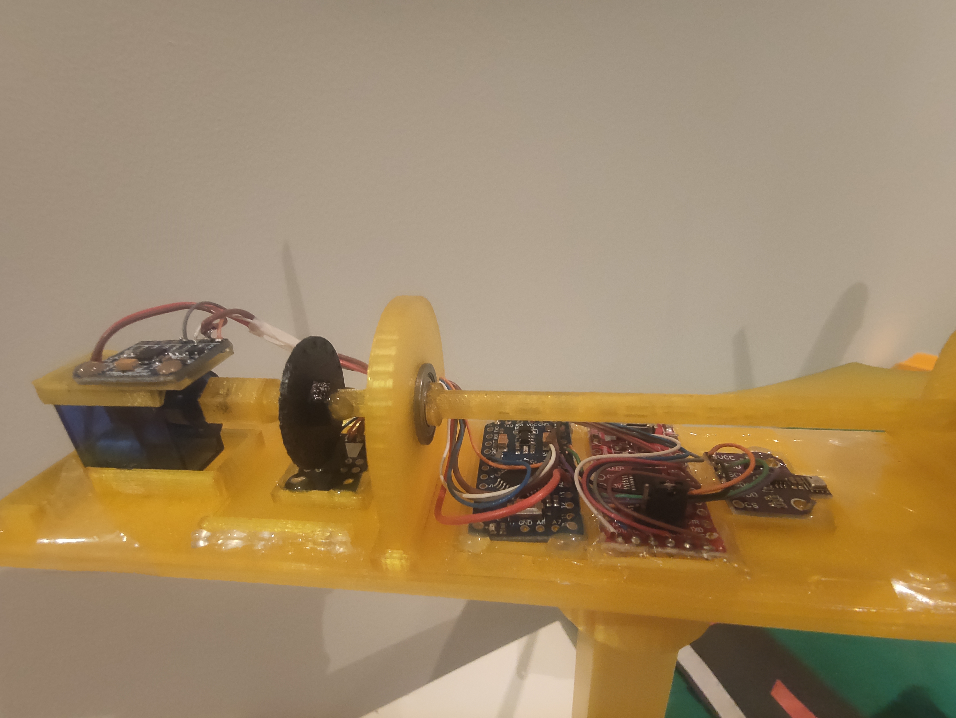
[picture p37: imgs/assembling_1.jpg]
        
      </td>
      <td>
        
      </td>
      <td>
        
      </td>
    </tr>
    <tr>
      <td>
        
      </td>
      <td>
        
      </td>
      <td>
        
      </td>
    </tr>
    <tr>
      <td>
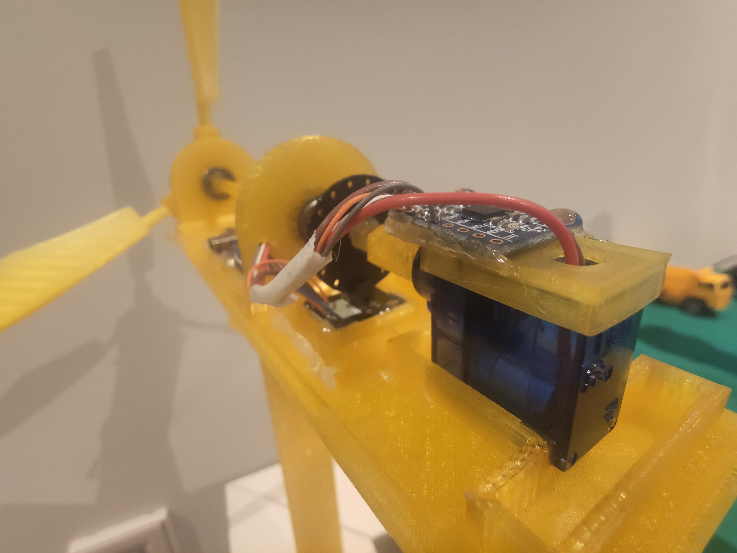
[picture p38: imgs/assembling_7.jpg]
        
      </td>
      <td>
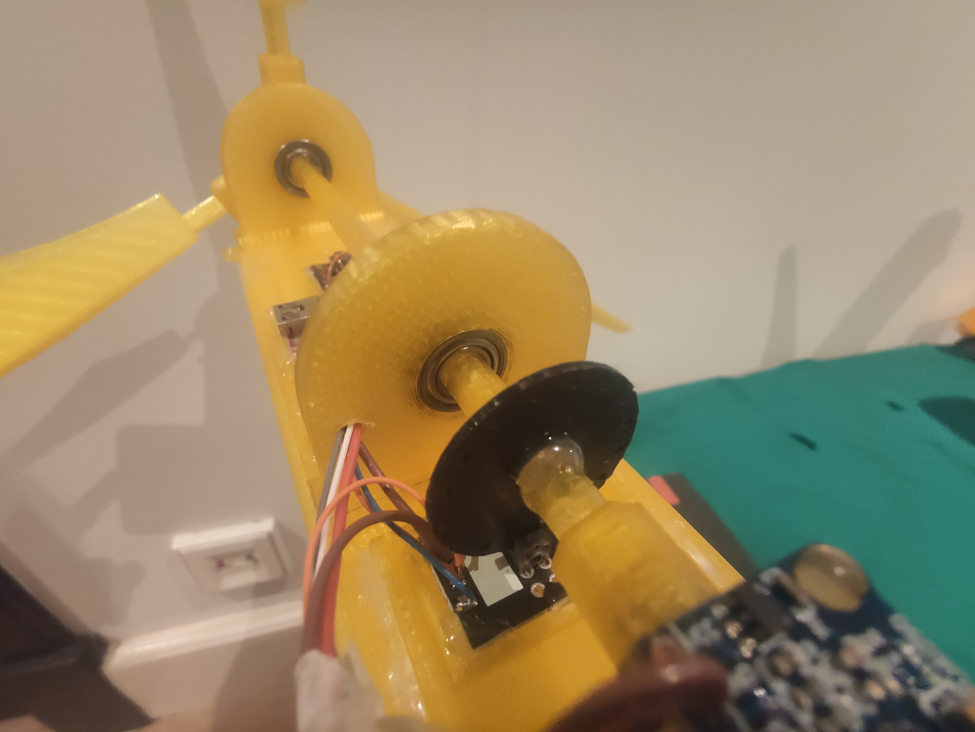
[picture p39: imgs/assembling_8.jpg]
        
      </td>
      <td>
        
      </td>
    </tr>
  </table>  

After building your turbine, plug it to your computer and [follow these instructions](02_Firmware/README.md) to compile the firmware and flash it to the arduino. 

## Wind speed meter

You can also build your own wind speed meter, that can be attached to the top cover of the wind turbine. This is another sensor, required to analize the wind turbine performance and some potential anomalies. It uses the same infrared sensor to measure the speed of the turbine rotor. As you can see in the schematics, this sensor's signal is also read by Arduino and sent to your edge device through the same communication channel.

<p align="center">
  <table border="0" align="center">
    <tr>
      <td>
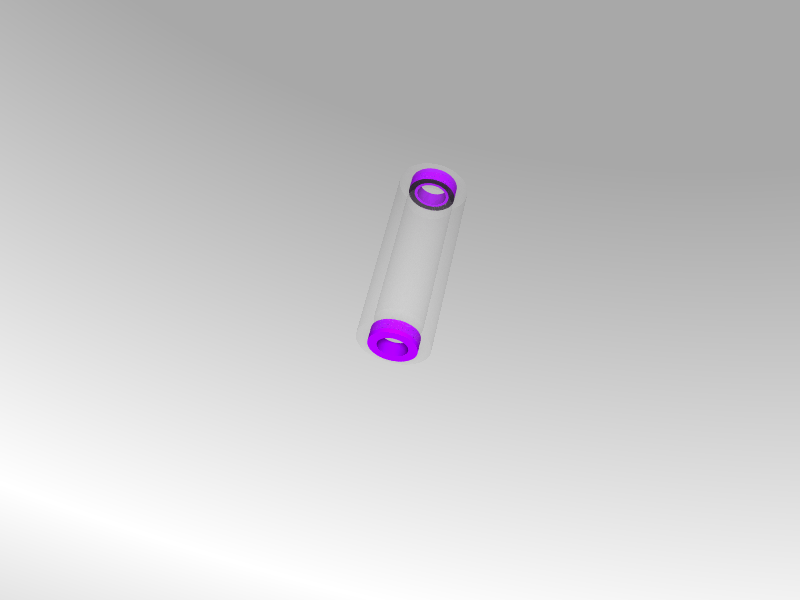
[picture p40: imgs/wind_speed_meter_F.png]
        
      </td>
      <td>
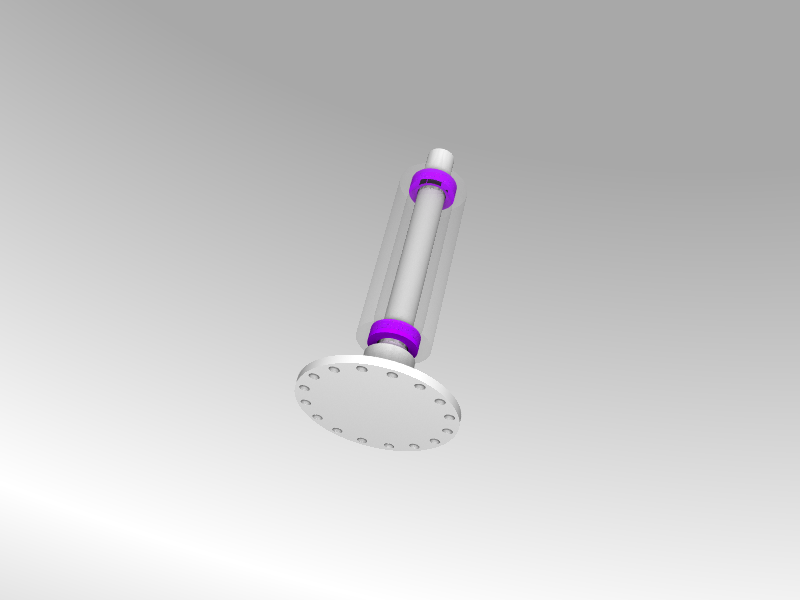
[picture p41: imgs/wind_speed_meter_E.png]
        
      </td>
    </tr>
    <tr>
      <td>
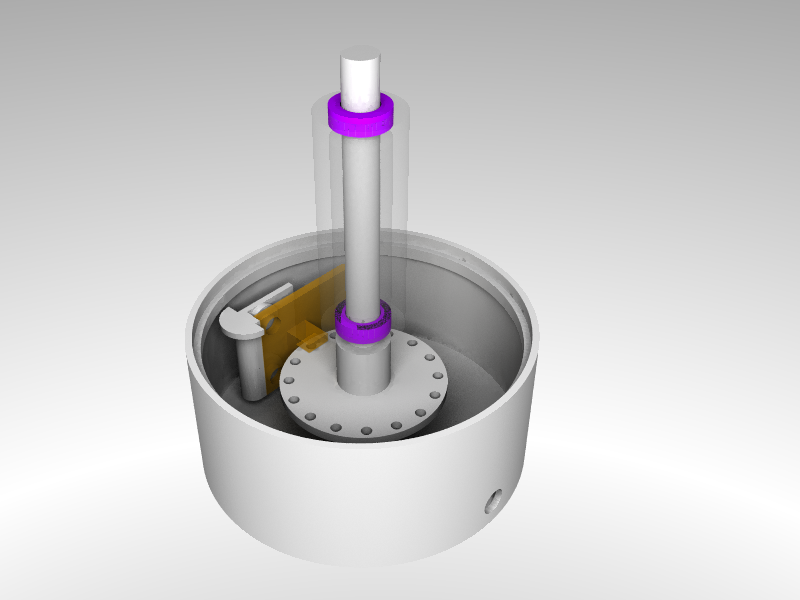
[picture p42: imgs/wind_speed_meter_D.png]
        
      </td>
      <td>
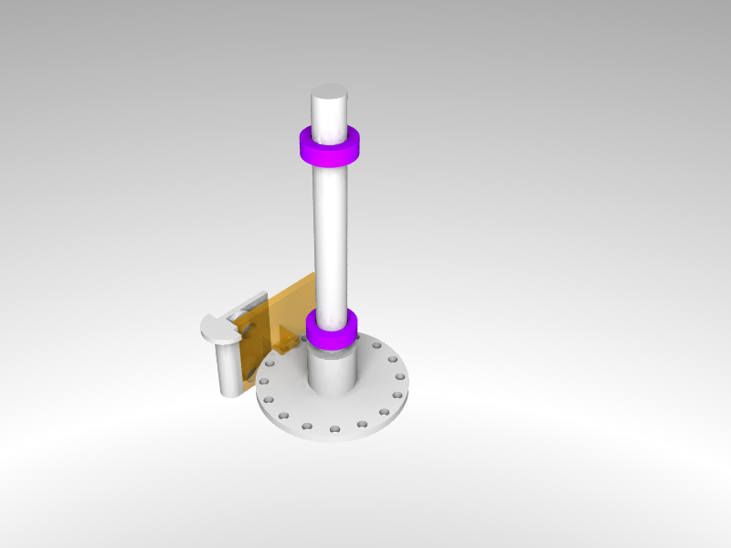
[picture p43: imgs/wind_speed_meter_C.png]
        
      </td>
    </tr>
    <tr>
      <td>
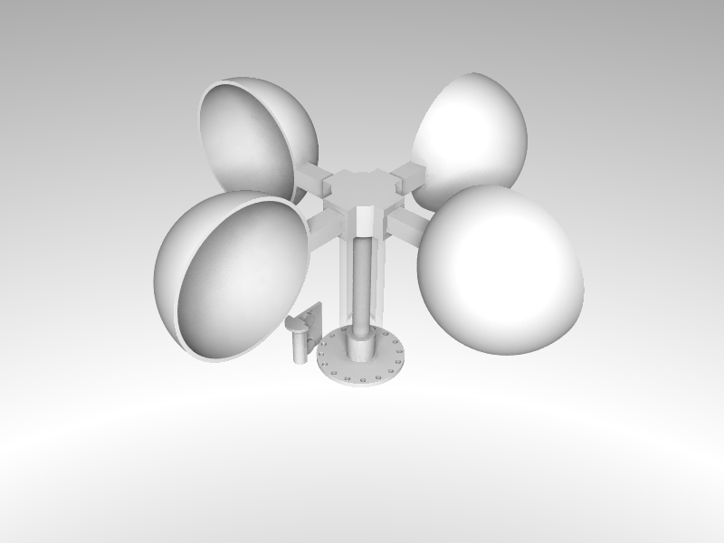
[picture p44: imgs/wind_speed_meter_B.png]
        
      </td>
      <td>
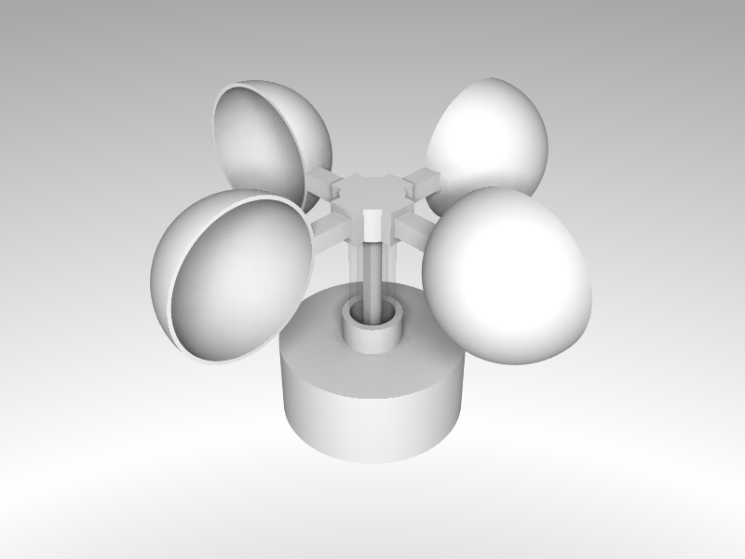
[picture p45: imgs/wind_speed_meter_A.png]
        
      </td>
    </tr>
  </table>  
</p>

Get and 3D print the following parts:
 - [Rotor](01_3DModels/wind_speed_stl/rotor.stl)
 - [Box cover](01_3DModels/wind_speed_stl/box_cover.stl)
 - [Light encoder disc](01_3DModels/wind_speed_stl/light_disc.stl)
 - [Infrared sensor support](01_3DModels/wind_speed_stl/light_sensor_support.stl)
 - [Shaft](01_3DModels/wind_speed_stl/shaft.stl)
 - [Shaft cover](01_3DModels/wind_speed_stl/shaft_cover.stl)
 - [Blade x4](01_3DModels/wind_speed_stl/blade.stl)
 - [Box](01_3DModels/wind_speed_stl/box.stl)

Other parts, required for building your wind speed sensor:
  - **Speed Encoder - Photo interrupter [Keyes K-010](https://www.amazon.de/-/en/AZDelivery-Sensor-Parent-KY-Kit/dp/B07DQLPZYF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)**: To count how many rotations per second 
  - **Mini Bearing - [Pack of 10 MR85ZZ Mini Ball Bearing Double Shielded Ball Bearings for 3D Printer Model 5x8x2,5 mm](https://www.amazon.de/gp/product/B07CKN7NPK/ref=ppx_yo_dt_b_asin_title_o02_s00?ie=UTF8&psc=1) x2**: two ball bearings to connect the shaft to the rotor.

To assemble it, just put pressure on some parts to attach them on each other. Use **hot glue** to fix the speed encoder and the support.

The **pink** elements are the bearings. They need to be attached to the shaft cover. The **yellow** component is the infrared sensor, that needs to be hot glued to the infrared sensor support. This support is hot glued to the box cover.

----

Finally, connect your WindTurbine to your Jetson Nano and then prepare it with [the application](04_EdgeApplication/).

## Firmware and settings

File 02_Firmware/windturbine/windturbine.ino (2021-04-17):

#include "Adafruit_BME680.h" // version 1.1.1
/// ATTENTION: You need to edit Adafruit_BME680.cpp and comment line 129 --> //_wire->begin();

#include "MPU6050_6Axis_MotionApps_V6_12.h"

#define LIGHT_PIN 2
#define LIGHT_WIND_SPEED_PIN 8
#define VOLTAGE_PIN A0
#define BAUD_RATE 115200
#define BME_CHECK_INTERVAL_MS 10000
#define ROTATION_CHECK_INTERVAL_MS 1000
#define MPU_CHECK_INTERVAL_MS 50

int voltage = 0, errorCode = 0;
uint16_t packetSize;
uint8_t fifoBuffer[64];
char userCommand[] = {' ', '\0'} ;
unsigned long last_bme_check = 0;
unsigned long last_mpu_check = 0;
unsigned long last_rot_check = 0;
float rps = 0; float wind_speed_rps = 0; // rotations per second
int rotation_counter = 0;
int prev_rot_status = 0;
int wind_speed_rotation_counter = 0;
int prev_wind_speed_status = 0;


Quaternion q;
VectorFloat gravity;
VectorInt16 aa;
float currTemp=0;
float temp, humidity, pressure, gas;  // BME readings  

//BME680_Class BME680;  ///< Create an instance of the BME680 class
Adafruit_BME680 bme; // I2C
MPU6050 mpu;

extern char *__brkval;
int freeMemory() {char top; return &top - __brkval;}

void setup() {
  Wire.setClock(200000); // 400kHz I2C clock (200kHz if CPU is 8MHz)
  
  Serial.begin(BAUD_RATE);
  while (Serial.available() && Serial.read()); // empty buffer

  pinMode(VOLTAGE_PIN, INPUT);
  pinMode(LIGHT_PIN, INPUT);
  pinMode(LIGHT_WIND_SPEED_PIN, INPUT);

  if (!bme.begin()) {
    errorCode = 1;
    return;
  }

  mpu.initialize();
  // verify connection
  if (!mpu.testConnection()) {
    // Device communication error
    errorCode = 2;
    return;
  } // if

  // load and configure the DMP
  if (mpu.dmpInitialize() != 0 ) {
    // DMP initialization error
    errorCode = 3;
    return;
  } // if  

  // supply your own gyro offsets here, scaled for min sensitivity
  mpu.setXGyroOffset(-616);
  mpu.setYGyroOffset(-46);
  mpu.setZGyroOffset(5);
  mpu.setXAccelOffset(-1430);
  mpu.setYAccelOffset(-552);
  mpu.setZAccelOffset(1276);
  // Calibration Time: generate offsets and calibrate our MPU6050
  mpu.CalibrateAccel(6);
  mpu.CalibrateGyro(6);
  
  mpu.setDMPEnabled(true);
  
  // get expected DMP packet size for later comparison
  packetSize = mpu.dmpGetFIFOPacketSize();  

//  // Set up oversampling and filter initialization
  bme.setTemperatureOversampling(BME680_OS_8X);
  bme.setHumidityOversampling(BME680_OS_2X);
  bme.setPressureOversampling(BME680_OS_4X);
  bme.setIIRFilterSize(BME680_FILTER_SIZE_3);
  bme.setGasHeater(320, 150); // 320*C for 150 ms
}

void loop() {
  if (errorCode != 0 ) {
    // keep sending the error signal
    Serial.print("Invalid Intialization. Please fix that and restart. Code: ");
    Serial.println(errorCode);
    delay(3000);
    return;
  } // if

  // read command from host
  if (Serial.available()) {
    int counter = 0;
    while (Serial.available()) {
      char b = Serial.read();
      if ( counter == 0 ) userCommand[0] = b;
      ++counter; // ignore the rest of the characters
    } // while    
  } // if

  bool has_new_data = false;
  if (millis() - last_mpu_check > MPU_CHECK_INTERVAL_MS ) {
    // read a packet from FIFO
    if (mpu.dmpGetCurrentFIFOPacket(fifoBuffer)) {
        // read a packet from FIFO
        mpu.dmpGetQuaternion(&q, fifoBuffer);
        mpu.dmpGetAccel(&aa, fifoBuffer);    
        mpu.dmpGetGravity(&gravity, &q);    
        currTemp = float(mpu.getTemperature())/340.0 + 36.53;
        last_mpu_check = millis();
        has_new_data = true;
    } // if
  } // if
      
  voltage = analogRead(VOLTAGE_PIN);
  int rot_status = digitalRead(LIGHT_PIN);
  int wind_speed_status = digitalRead(LIGHT_WIND_SPEED_PIN);

  if (prev_wind_speed_status != wind_speed_status && wind_speed_status == 0 ) {
    wind_speed_rotation_counter += 1;
  } // if
  prev_wind_speed_status = wind_speed_status;
  
  if (prev_rot_status != rot_status && rot_status == 0 ) {
    rotation_counter += 1;
  } // if
  prev_rot_status = rot_status;
  
  if ( millis() - last_rot_check > ROTATION_CHECK_INTERVAL_MS ) {
    rps = float(rotation_counter) / 16;
    wind_speed_rps = float(wind_speed_rotation_counter) / 16;
    wind_speed_rotation_counter = 0;
    rotation_counter = 0;
    last_rot_check = millis();
    has_new_data = true;
  }

  if (millis() - last_bme_check > BME_CHECK_INTERVAL_MS && bme.remainingReadingMillis() == -1) {
    last_bme_check = millis();
    bme.beginReading();    
  }

  if (bme.remainingReadingMillis() == 0) {
      bme.endReading();
      temp = bme.temperature;
      pressure = bme.pressure / 100.0;
      humidity = bme.humidity;
      gas = bme.gas_resistance / 1000.0;
      has_new_data = true;
  }

  if (!has_new_data) return;
  
  Serial.print(millis()); Serial.print(',');
  Serial.print(freeMemory()); Serial.print(',');

  Serial.print(rps);Serial.print(',');
  Serial.print(wind_speed_rps);Serial.print(',');
  Serial.print(voltage);Serial.print(',');
  Serial.print(q.w); Serial.print(',');
  Serial.print(q.x); Serial.print(',');
  Serial.print(q.y); Serial.print(',');
  Serial.print(q.z); Serial.print(',');
  Serial.print(gravity.x); Serial.print(',');
  Serial.print(gravity.y); Serial.print(',');
  Serial.print(gravity.z); Serial.print(',');
  Serial.print(aa.x); Serial.print(',');
  Serial.print(aa.y); Serial.print(',');
  Serial.print(aa.z); Serial.print(',');
  Serial.print(currTemp); Serial.print(',');  
  Serial.print(temp); Serial.print(',');
  Serial.print(humidity); Serial.print(',');
  Serial.print(pressure); Serial.print(','); 
  Serial.print(gas/100);   
  Serial.print('\n');

}

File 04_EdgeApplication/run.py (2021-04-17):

#!/usr/bin/python3
# Copyright Amazon.com, Inc. or its affiliates. All Rights Reserved.
# SPDX-License-Identifier: MIT-0
import os
import numpy as np
import io
import serial
import json
import logging
import argparse
import time
import requests
import gzip

import turbine

from datetime import datetime

if __name__ == '__main__':
    # parse the input parameters    
    parser = argparse.ArgumentParser()

    parser.add_argument('--test-mode', action="store_true", help="Use a dummy file as sensors readings")
    parser.add_argument('--inject-noise', action="store_true", help="Add random noise to the raw data")
    parser.add_argument("--debug", action="store_true", help='Enable debugging messages')    

    parser.add_argument('--agent-socket', type=str, default="/tmp/edge_agent", help='The unix socket path created by the agent')
    parser.add_argument('--model-path', type=str, default=os.path.join(os.environ["SM_EDGE_AGENT_HOME"], 'models'), help='Absolute path to the model dir')

    parser.add_argument('--serial-port', type=str, default="/dev/ttyUSB0", help='Path to the USB port used by the wind turbine')
    parser.add_argument('--serial-baud', type=int, default=115200, help='Serial comm. speed in bits per second')

    parser.add_argument('--sagemaker-edge-configfile-path', type=str, default=os.path.join(os.environ["SM_EDGE_AGENT_HOME"], "sagemaker_edge_config.json"), help='Path to the agent config file')

    args = parser.parse_args()
    logging.basicConfig(level=logging.DEBUG if args.debug else logging.INFO )
    logging.debug("Parsing parameters")

    # load sagemaker edge agent config file
    iot_params = json.loads(open(args.sagemaker_edge_configfile_path, 'r').read())

    # retrieve the IoT thing name associated with the edge device
    iot_client = turbine.get_client('iot', iot_params)
    sm_client = turbine.get_client('sagemaker', iot_params)
    resp = sm_client.describe_device(
        DeviceName=iot_params['sagemaker_edge_core_device_uuid'], 
        DeviceFleetName=iot_params['sagemaker_edge_core_device_fleet_name']
    )    
    device_name = resp['IotThingName']
    mqtt_host=iot_client.describe_endpoint(endpointType='iot:Data-ATS')['endpointAddress']
    mqtt_port=8883

    # buffer size required to process timeseries data
    PREDICTIONS_INTERVAL = 1.0 # interval in seconds between the predictions
    MIN_NUM_SAMPLES = 500         
    INTERVAL = 5 # seconds
    TIME_STEPS = 20 * INTERVAL
    STEP = 10
    FEATURES_IDX = [6,7,8,5,  3, 2, 4] # qX,qy,qz,qw  ,wind_seed_rps, rps, voltage 
    NUM_RAW_FEATURES = 20
    NUM_FEATURES = 6

    # Some constants used for data prep + compare the results
    thresholds = np.load('statistics/thresholds.npy')
    raw_std = np.load('statistics/raw_std.npy')
    mean = np.load('statistics/mean.npy')
    std = np.load('statistics/std.npy')

    logging.info("Initializing...")
    # Sends the logs to the cloud via MQTT Topics
    logger = turbine.Logger(device_name, iot_params)

    # Initialize the Edge Manager agent
    edge_agent = turbine.EdgeAgentClient(args.agent_socket)
    
    model_loaded = False
    model_name = None
    def model_update_callback(name, version):
        global model_loaded, model_name
        model_version=str(version)
        model_name = "%s-%s" % (name, model_version.replace('.', '-')) 
        logging.info('New model deployed: %s - %s - %s' % (name, model_version, model_name))
        resp = edge_agent.load_model(model_name, os.path.join(args.model_path, name, model_version))
        if resp is None: 
            logging.error('It was not possible to load the model. Is the agent running?')
            return
        model_loaded = True 

    ## Initialize the OTA Model Manager
    model_manager = turbine.OTAModelUpdate(device_name, iot_params, mqtt_host, mqtt_port, model_update_callback, args.model_path)
   
    ## Initialize sensors reader
    if args.test_mode:
        logging.info('Using Dummy sensors readings')
        # use a local file to simulate the raw data collected from the turbine's sensors
        if not os.path.exists('dataset_wind.csv'):
            req = requests.get('https://aws-ml-blog.s3.amazonaws.com/artifacts/monitor-manage-anomaly-detection-model-wind-turbine-fleet-sagemaker-neo/dataset_wind_turbine.csv.gz')
            with gzip.GzipFile(fileobj=io.BytesIO(req.content), mode="r:gz") as f:
                with open('dataset_wind.csv', 'w') as d: d.write(f.read().decode('utf-8'))

        class DummySensors(object):
            def __init__(self):
                self.buffer = open('dataset_wind.csv', 'r').readlines()[1:] # skip the file header
                self.idx = 0
            def isOpen(self): return True
            def close(self): pass
            def readline(self):
                if self.idx >= len(self.buffer): self.idx = 0
                reading = self.buffer[self.idx].strip().split(',')[2:] # drop the first two columns
                reading = reading[0:2] + [reading[3], reading[-1]] + reading[4:-1] # reorganize the columns
                reading = ",".join(reading).encode('utf-8')
                self.idx += 1
                return reading

        turbine_sensors = DummySensors()
    else:
        logging.info('Reading from the sensors of the turbine')
        # Initialize the turbine program
        turbine_sensors = serial.Serial(port=args.serial_port, baudrate=args.serial_baud)

    logging.info("Defining parameters")

    # main loop
    samples = []
    logging.info("Starting main loop..")
    try:
        while turbine_sensors.isOpen(): # runs while it communicates with the arduino
            if not model_loaded:
                logging.info("Waiting for the model...")
                time.sleep(5)
                continue

            # get the (raw) sensors data
            data = ""
            try:
                data = turbine_sensors.readline().decode('utf-8').strip()
                tokens = np.array(data.split(','))
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
